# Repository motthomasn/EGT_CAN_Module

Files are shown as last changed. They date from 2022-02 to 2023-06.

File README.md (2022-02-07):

# EGT_CAN_Module
Teensy 3.2 based controller board designed to amplify K-Type thermocouple signals and transmit the data digitally via CAN-Bus

This module was built for a turbocharged motorcycle project but has been repurposed for a number of other applications. The aim was to have a flexible method of amplifying signals from K-Type thermocouples and transmitting the data digitally via CAN-Bus to an ECU or datalogger.

The module uses 5off Maxim MAX31855 digital thermocouple converters to process the K-Type signals and a Teensy 3.2 development board to retrieve & broadcast the data. The allowance for 5off K-Type sensors was included specifically for turbocharged 4 cylinder applications (4off port temperatures and 1off turbine inlet temperature), however if fewer sensors are needed then the additional amplifier IC's can just be omitted and the code adjusted to compensate.

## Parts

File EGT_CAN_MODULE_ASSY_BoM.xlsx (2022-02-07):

Designation | Description | Value | Manufacturer | Part Number | Package | Supplier | Stock No. / Order Code
U1 | Teensy 3.2 |  | PJRC | Teensy 3.2 | PDIP | HobbyTronics
 | Teensy Connector Socket | 14-way, 1 Row, 2.54mm Socket | Harwin | M20-7823646 |  | RS | 488-1724
U2 | Board Power Regulator | 5V, 1A | Traco Power | TSR 1-2450 | SIP 3 | RS | 666-4379
U3 | CAN Transceiver |  | Microchip | MCP2551-I/SN | SOIC 8 | RS | 738-6036
U4,U5,U6,U7,U8 | K-Type Thermocouple Amplifier |  | Maxim Integrated | MAX31855KASA+ | SOIC 8 | RS | 786-1017
C1 | Power Reg Smoothing Cap | 22µF | Murata | GRM219B30G226ME66D | 0805 | RS | 798-4624
C2 | CAN Transciever Input Smoothing Cap | 100nF | AVX | 08055C104KAT2A | 0805 | RS | 464-6688
C3,C4,C5,C6,C7 | Amplifier Input Smoothing Cap | 100nF | AVX | 08055C104KAT2A | 0805 | RS | 464-6688
C8, C9, C10, C11, C12 | K-Type Noise Filter Cap | 10nF | AVX | 08055C103KAT2A | 0805 | RS | 464-6672
R1 | CAN Transciever Reset Resistor | 18K | TE Connectivity | CRG0805F18K | 0805 | RS | 223-0590
R2 | CAN Termination Resistor | 120 | Panasonic | ERJP06F1200V | 0805 | RS | 721-7674
SW1 | CAN Termination Resistor Switch | Single SPST | APEM | IKD0103101 |  | RS | 877-2233
P1 | K-Type Interface Connector
P2 | Board Connector | 4-Way, 2 Row, 2.54mm Right Angle Pin Header | RS PRO | 251-8660 |  | RS | 251-8660

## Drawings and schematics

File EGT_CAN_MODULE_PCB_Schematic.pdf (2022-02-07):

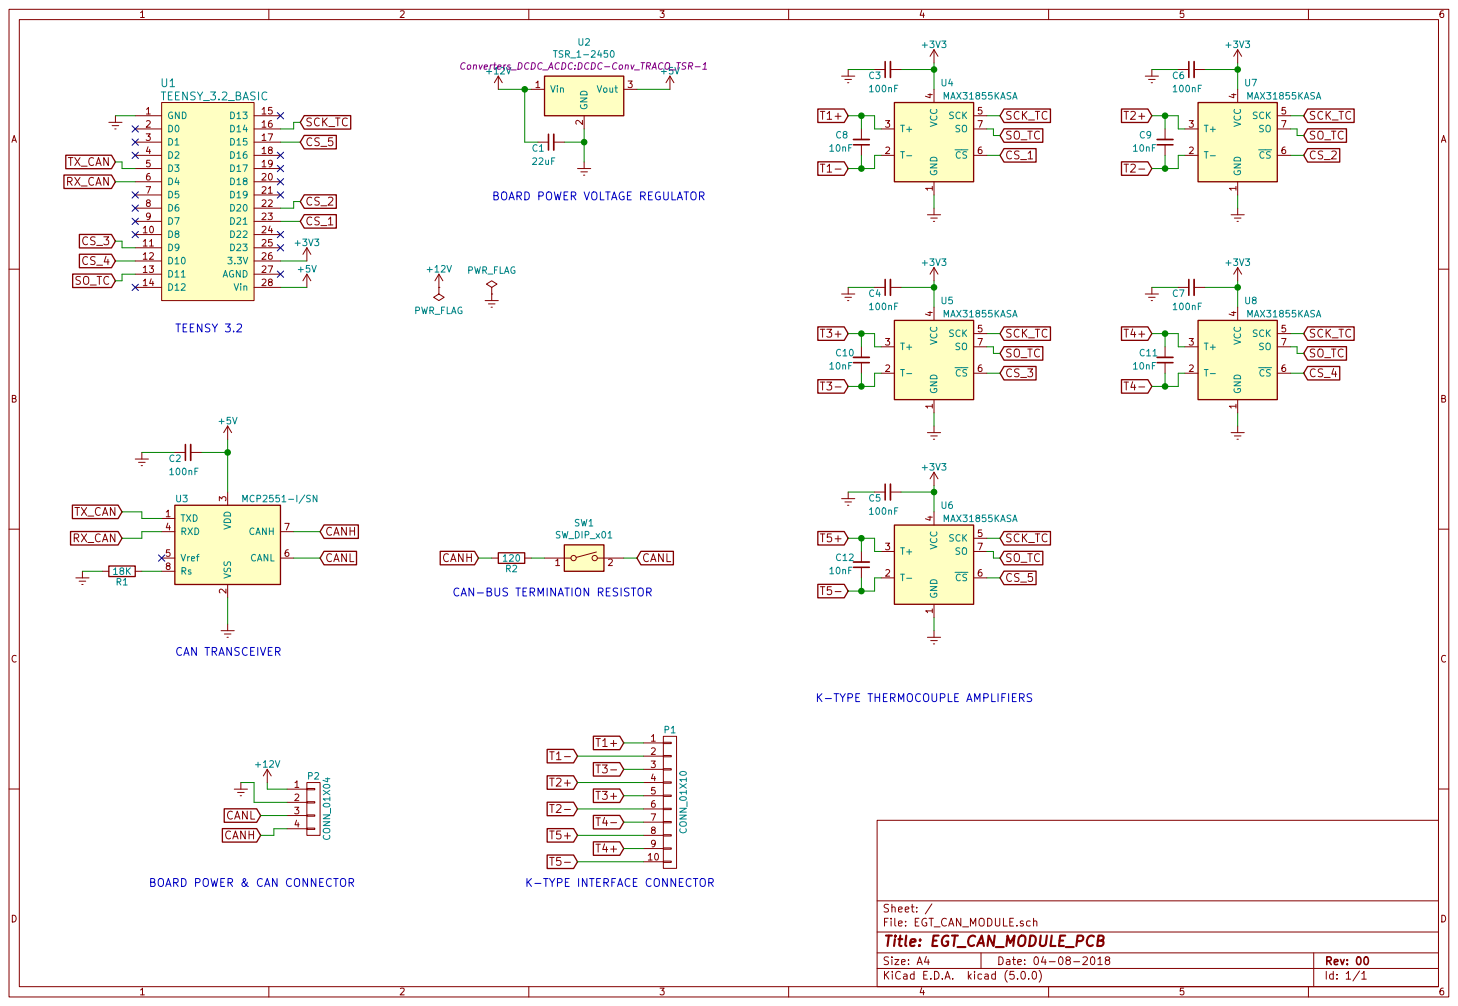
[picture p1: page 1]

BOARD POWER VOLTAGE REGULATOR

3 RXD 4 Vref 5 CANL 6 CANH 7 Rs 8 U3 MCP2551-I/SN RX_CAN
TX_CAN

CAN-BUS TERMINATION RESISTOR

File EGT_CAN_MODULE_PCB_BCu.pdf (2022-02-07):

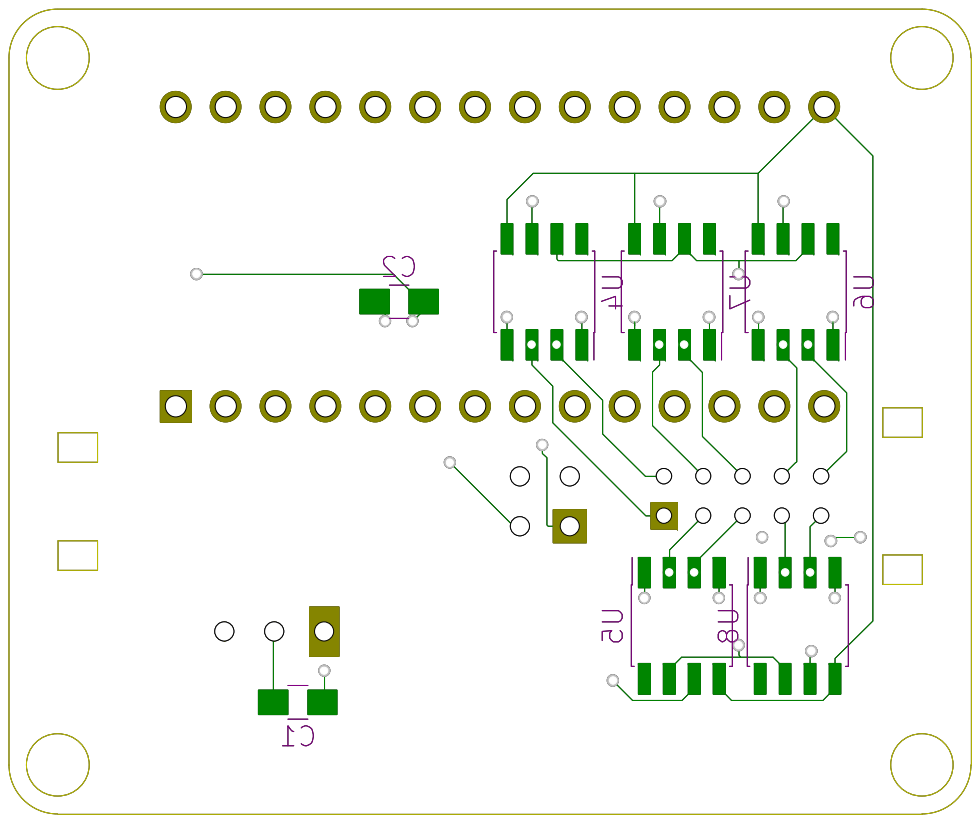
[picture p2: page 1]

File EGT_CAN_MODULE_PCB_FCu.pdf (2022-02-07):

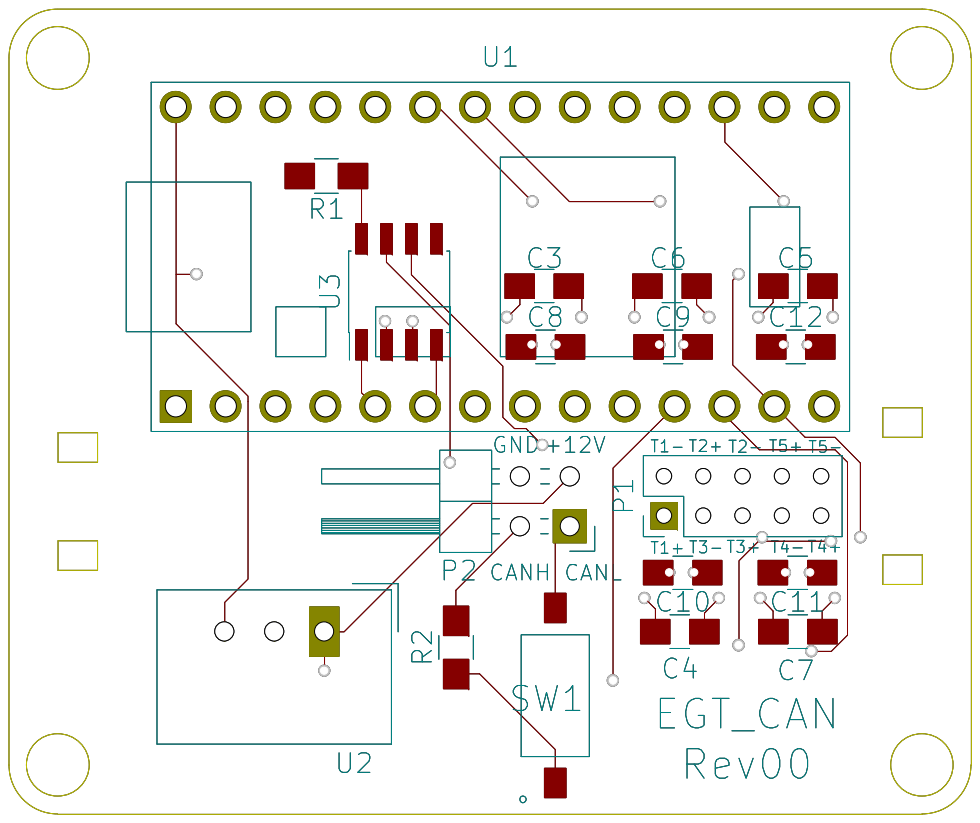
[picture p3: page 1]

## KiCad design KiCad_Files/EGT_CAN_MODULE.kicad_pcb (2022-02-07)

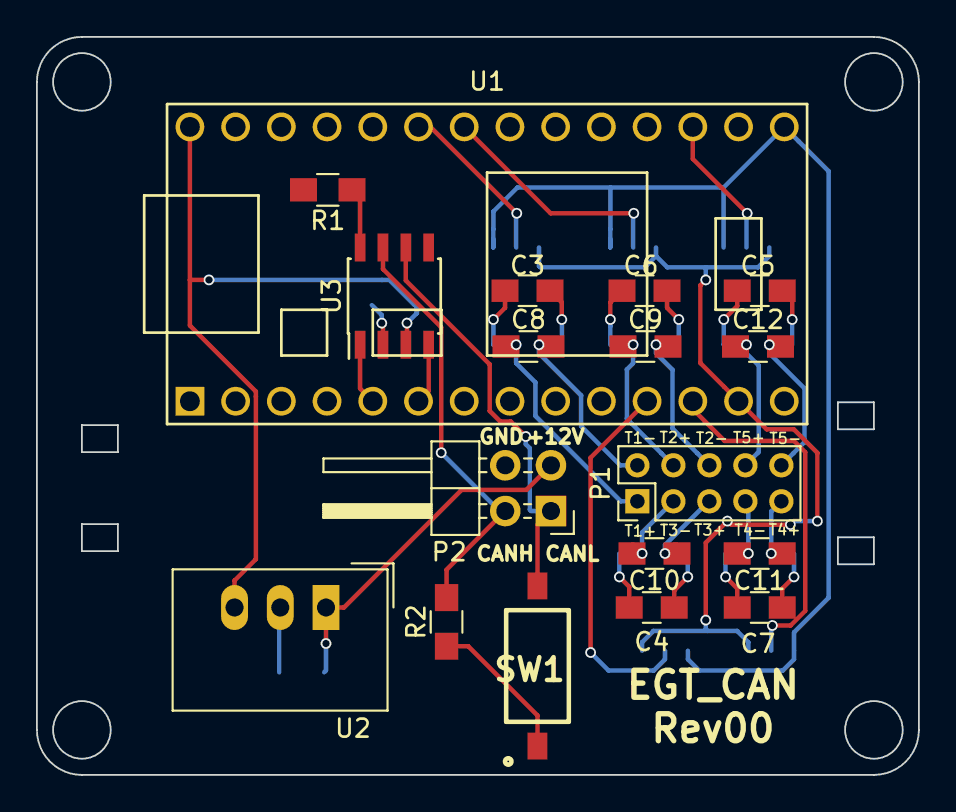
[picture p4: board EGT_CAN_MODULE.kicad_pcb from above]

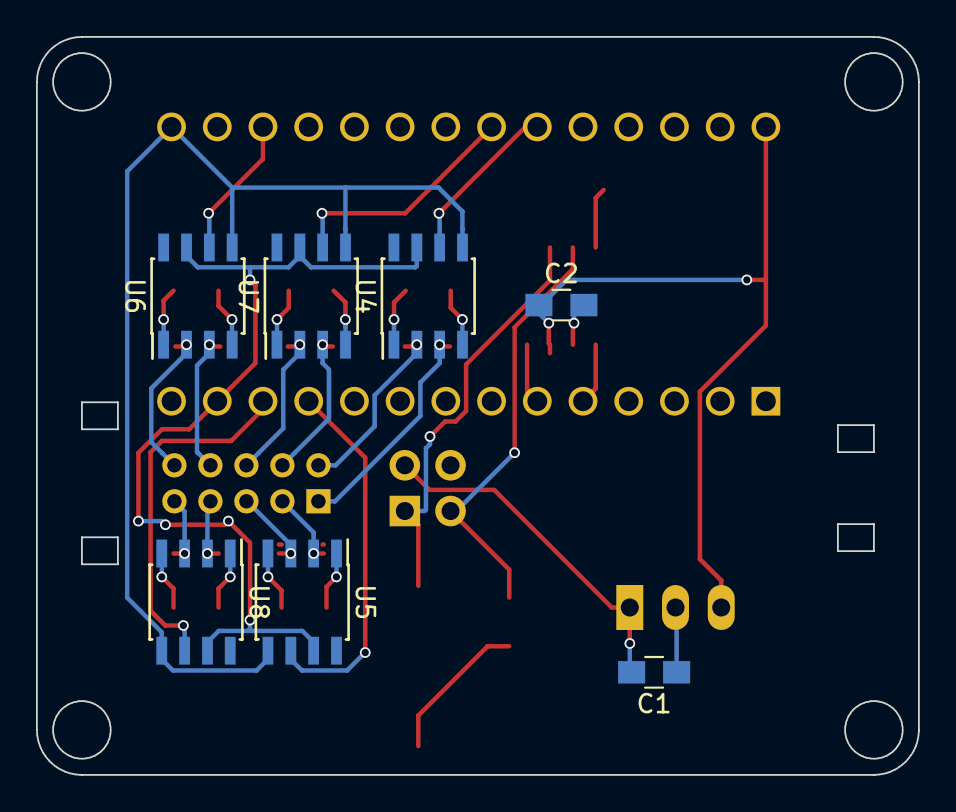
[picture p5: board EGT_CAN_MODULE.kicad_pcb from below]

Board: 2 copper layers, 49.0 x 41.0 mm, 25 parts (7 on the bottom side), 27 nets.

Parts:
C1: 22uF; C_0805_HandSoldering
C2, C3, C4, C5, C6, C7: 100nF; C_0805_HandSoldering
C8, C9, C10, C11, C12: 10nF; C_0805_HandSoldering
P1: CONN_01X10; Pin_Header_Straight_2x05_Pitch2.00mm
P2: CONN_01X04; Pin_Header_Angled_2x02_Pitch2.54mm
R1: 18K; R_0805_HandSoldering
R2: 120; R_0805_HandSoldering
SW1: SW_DIP_x01; IKD0103101
U1: TEENSY_3.2_BASIC
U2: TSR_1-2450; DCDC-Conv_TRACO_TSR-1
U3: MCP2551-I/SN; SOIC-8_3.9x4.9mm_Pitch1.27mm
U4, U5, U6, U7, U8: MAX31855KASA; SOIC-8_3.9x4.9mm_Pitch1.27mm

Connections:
+3V3: C3.2, C4.2, C5.2, C6.2, C7.2, U1.26, U4.4, U5.4, U6.4, U7.4, U8.4
+5V: C2.2, U1.28, U2.3, U3.3
+12V: C1.1, P2.1, U2.1
CANH: P2.4, R2.2, U3.7
CANL: P2.3, SW1.2, U3.6
CS_1: U1.23, U4.6
CS_2: U1.22, U7.6
CS_3: U1.11, U5.6
CS_4: U1.12, U8.6
CS_5: U1.17, U6.6
Earth: C1.2, C2.1, C3.1, C4.1, C5.1, C6.1, C7.1, P2.2, R1.2, U1.1, U2.2, U3.2, U4.1, U5.1, U6.1, U7.1, U8.1
unnamed: R1.1, U3.8
unnamed: R2.1, SW1.1
RX_CAN: U1.6, U3.4
SCK_TC: U1.16, U4.5, U5.5, U6.5, U7.5, U8.5
SO_TC: U1.13, U4.7, U5.7, U6.7, U7.7, U8.7
T1+: C8.2, P1.1, U4.3
T1-: C8.1, P1.2, U4.2
T2+: C9.2, P1.4, U7.3
T2-: C9.1, P1.6, U7.2
T3+: C10.2, P1.5, U5.3
T3-: C10.1, P1.3, U5.2
T4+: C11.2, P1.9, U8.3
T4-: C11.1, P1.7, U8.2
T5+: C12.2, P1.8, U6.3
T5-: C12.1, P1.10, U6.2
TX_CAN: U1.5, U3.1

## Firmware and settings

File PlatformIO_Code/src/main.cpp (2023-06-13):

/*
 * Copyright 2018 THOMAS NAUGHTON <motthomasn@gmail.com>
 * 
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
 * The above copyright notice and this permission notice shall be included in all copies or substantial portions of the Software.
 * 
 * THE SOFTWARE IS PROVIDED "AS IS", WITHOUT WARRANTY OF ANY KIND, EXPRESS OR IMPLIED, INCLUDING BUT NOT LIMITED TO THE WARRANTIES OF MERCHANTABILITY, 
 * FITNESS FOR A PARTICULAR PURPOSE AND NONINFRINGEMENT. IN NO EVENT SHALL THE AUTHORS OR COPYRIGHT HOLDERS BE LIABLE FOR ANY CLAIM, DAMAGES OR OTHER LIABILITY, 
 * WHETHER IN AN ACTION OF CONTRACT, TORT OR OTHERWISE, ARISING FROM, OUT OF OR IN CONNECTION WITH THE SOFTWARE OR THE USE OR OTHER DEALINGS IN THE SOFTWARE.
 */

/*
 * EGT_CAN_MODULE_ASSY_CODE
 * Version 1.0      22-08-2019      Original generic code for Teensy 3.2 controller. Based on Microsquirt_EGT_CAN_Module_Timer.ino code
 * Version 1.1      04-06-2020      Code adjusted to suit Platform IO IDE & Life Racing F88R ECU installation
 * Version 1.2      09-05-2023      CAN ID adjusted to match CAN Config v3.0
 * 
 * This code is designed for use with the 015-0011 K-TYPES MODULE ASSY utilising 015-0012 R00 PCB layout
 * CAN Config:  200507_LOGGER_CAN_CONFIG_v2.0.xlsx
 * CAN DBC:     190820_Input_Config_v2.1.txt
 * Messages recieved are MSB First or Big Endian byte order
 * 
 * See documentation for details & overview
 */

#include <Arduino.h>

// CAN libraries
#include <FlexCAN.h>

// K-Type libraries
#include <SPI.h>
#include <Adafruit_MAX31855.h>
#include <Wire.h>

//===============================================================================================

// User Config variables
// Define variables most likely to be changed by user
#define MsgID 0x700       // CAN message ID
#define can_speed 500000 // CAN-Bus baud rate in bps
#define update_freq 2    // Update rate in Hz

// CAN Variables
static CAN_message_t txmsg;

// K-Type Variables
// Pin designations need to match PCB layout
#define TCSO 11
#define TCCLK 13
#define TC1CS 21
#define TC2CS 20
#define TC3CS 9
#define TC4CS 10
#define TC5CS 15

Adafruit_MAX31855 *TC[5] = {new Adafruit_MAX31855(TCCLK, TC1CS, TCSO), new Adafruit_MAX31855(TCCLK, TC2CS, TCSO), new Adafruit_MAX31855(TCCLK, TC3CS, TCSO), new Adafruit_MAX31855(TCCLK, TC4CS, TCSO), new Adafruit_MAX31855(TCCLK, TC5CS, TCSO)};

// Timer variables
int update_period, diff;
long prev_time, now_time;

//===============================================================================================
void CAN_Send()
{

  // Send data
  Can0.write(txmsg);
}

//===============================================================================================
void UpdateTC()
{
  // Read data from each K-Type in turn & write data to tx buffer for sending via CAN
  for (int k = 0; k < 4; k++)
  {
    //int16_t EGT = ( (*TC[k]).readCelsius() );
    int16_t EGT = ((*TC[k]).readCelsius() * 10);
    //Serial.println(EGT);

    // Split into bytes and load into CAN message as we go
    // Data loaded MSB first or Big Endian
    txmsg.buf[k * 2 + 1] = byte(EGT & 0x00ffUL);
    txmsg.buf[k * 2] = byte((EGT & 0xff00UL) >> 8);
  }

  CAN_Send(); // once data is collected, send message
}

//===============================================================================================
// the setup routine runs once when you press reset:
void setup()
{
  //Serial.begin(115200); // only used for USB debugging

  //CAN setup
  Can0.begin(can_speed);

  txmsg.id = MsgID;
  txmsg.len = 8;

  update_period = (1000 / update_freq); // calculate update period in ms from frequency
  prev_time = 0;                        // initialise for timer
}

void loop()
{
  // Time for next record.
  now_time = millis();
  diff = (now_time - prev_time);

  if (diff >= update_period)
  {
    prev_time = now_time;

    UpdateTC();
  }
}
